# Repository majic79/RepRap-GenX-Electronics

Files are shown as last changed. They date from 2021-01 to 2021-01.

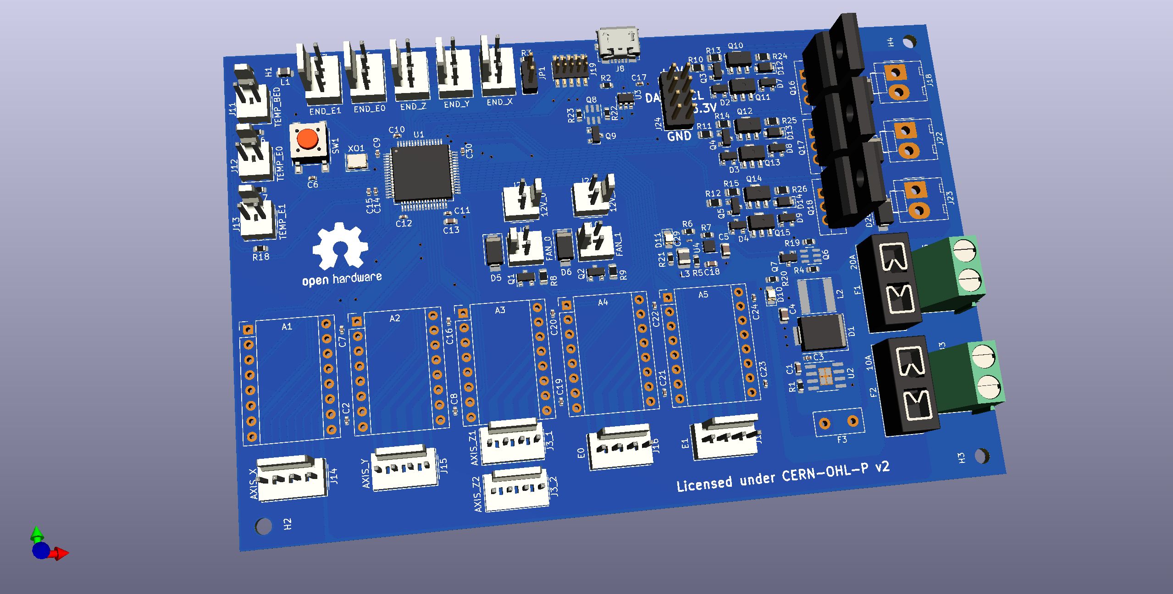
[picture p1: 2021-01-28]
RepRap_GenX_Electronics.png

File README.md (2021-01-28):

# RepRap GenX Electronics

## About
This project contains the hardware schematics and design choices for a low cost printer control board for RepRap hardware. Current boards are very capable, but make decisions on cost and feature set that are not of my choice. By making this available, I aim to add another option out there.

Making the printer control a drop in selection, this will permit re-use of existing driver breakouts (e.g. Pololu A4988's and DRV8825's) and with SPI support for TMC2300 breakouts, it allows an upgrade path. and low cost upgrade potential for existing printer controllers.

__!! Warning - this is still work in progress !!__

This board is based around the ARM MCU STM32F412RGT running at 96MHz in a LQFP-64 package. There are a few free pins, and with some ingenuity, some pins can be multiplexed/multi use.

## Plans

Future intent is to port MarlinFW to this package, from the PlatformIO platform. Programmers for these devices are relatively cheap, but there remains the possibility of a 0 cost programming option via the USB DFU device capabilties.

Selling these individually is not possible in todays marketplace without some additional testing and regulation, but those requirements need to be investigated and addressed as development progresses.

As the majority of components are surface mount (SMD) with only a few through-hole components, the plan is to complete the bill of materials (BOM) for the SMD components and send for professional fabrication on the prototypes.

## Milestones

  * ~~Initial Circuit~~
  * ~~MCU Selection~~
  * ~~Power Supplies~~
  * ~~PCB Layout~~
  * ~~RaspberryPi interface~~ (Abandoned due to lack of space for an interface)
  * ~~5V Power Output (on 2.54mm pitch 2x2 connector)~~
  * Review
  * Feedback
  * Component Selection (BOM)
  * Fabrication
  * Testing
  * Firmware Development

## News

### 2020-01-28
  - Added 3.3v and I2C to the breakout port for possible expansion
  - Shifted E0/E1 Filament sensor feedback to make room for I2C port
  - Adjusted some routes for the 2x4 breakout port

### 2020-01-26
  - Added totem pole drivers for the heater MOSFET's - switching time is <1uS so it should be possible to drive at 1MHz frequency if ever needed
  - Altered heater LED indicators to Red
  - Validated Fan PWM MOSFET's - 4mA is enough to drive at around 4uS which is plenty fast enough and won't overload GPIO pins
  - Altered layout to accomodate new components
  - Split MCU controlled components into their own sheet - not enough space on a single sheet for everything!

### 2020-01-21
  - Abandoned the idea of putting in a Pi Interface - difficult to maintain a 2 layer design and route everything for the 2x20pin GPIO interface of the Pi
  - Added ZVD Ideal diode for 5V output
  - Exposed 5V output (after ZVD) for external consumption (e.g. powering a Pi)
  - Added a copper pour on the top layer for an Earth plane
  - Re-Routed a few signals to maximise covered area on pour
  - Upped trace size for power lines to 0.8mm

### 2020-01-19
	- Initial Commit

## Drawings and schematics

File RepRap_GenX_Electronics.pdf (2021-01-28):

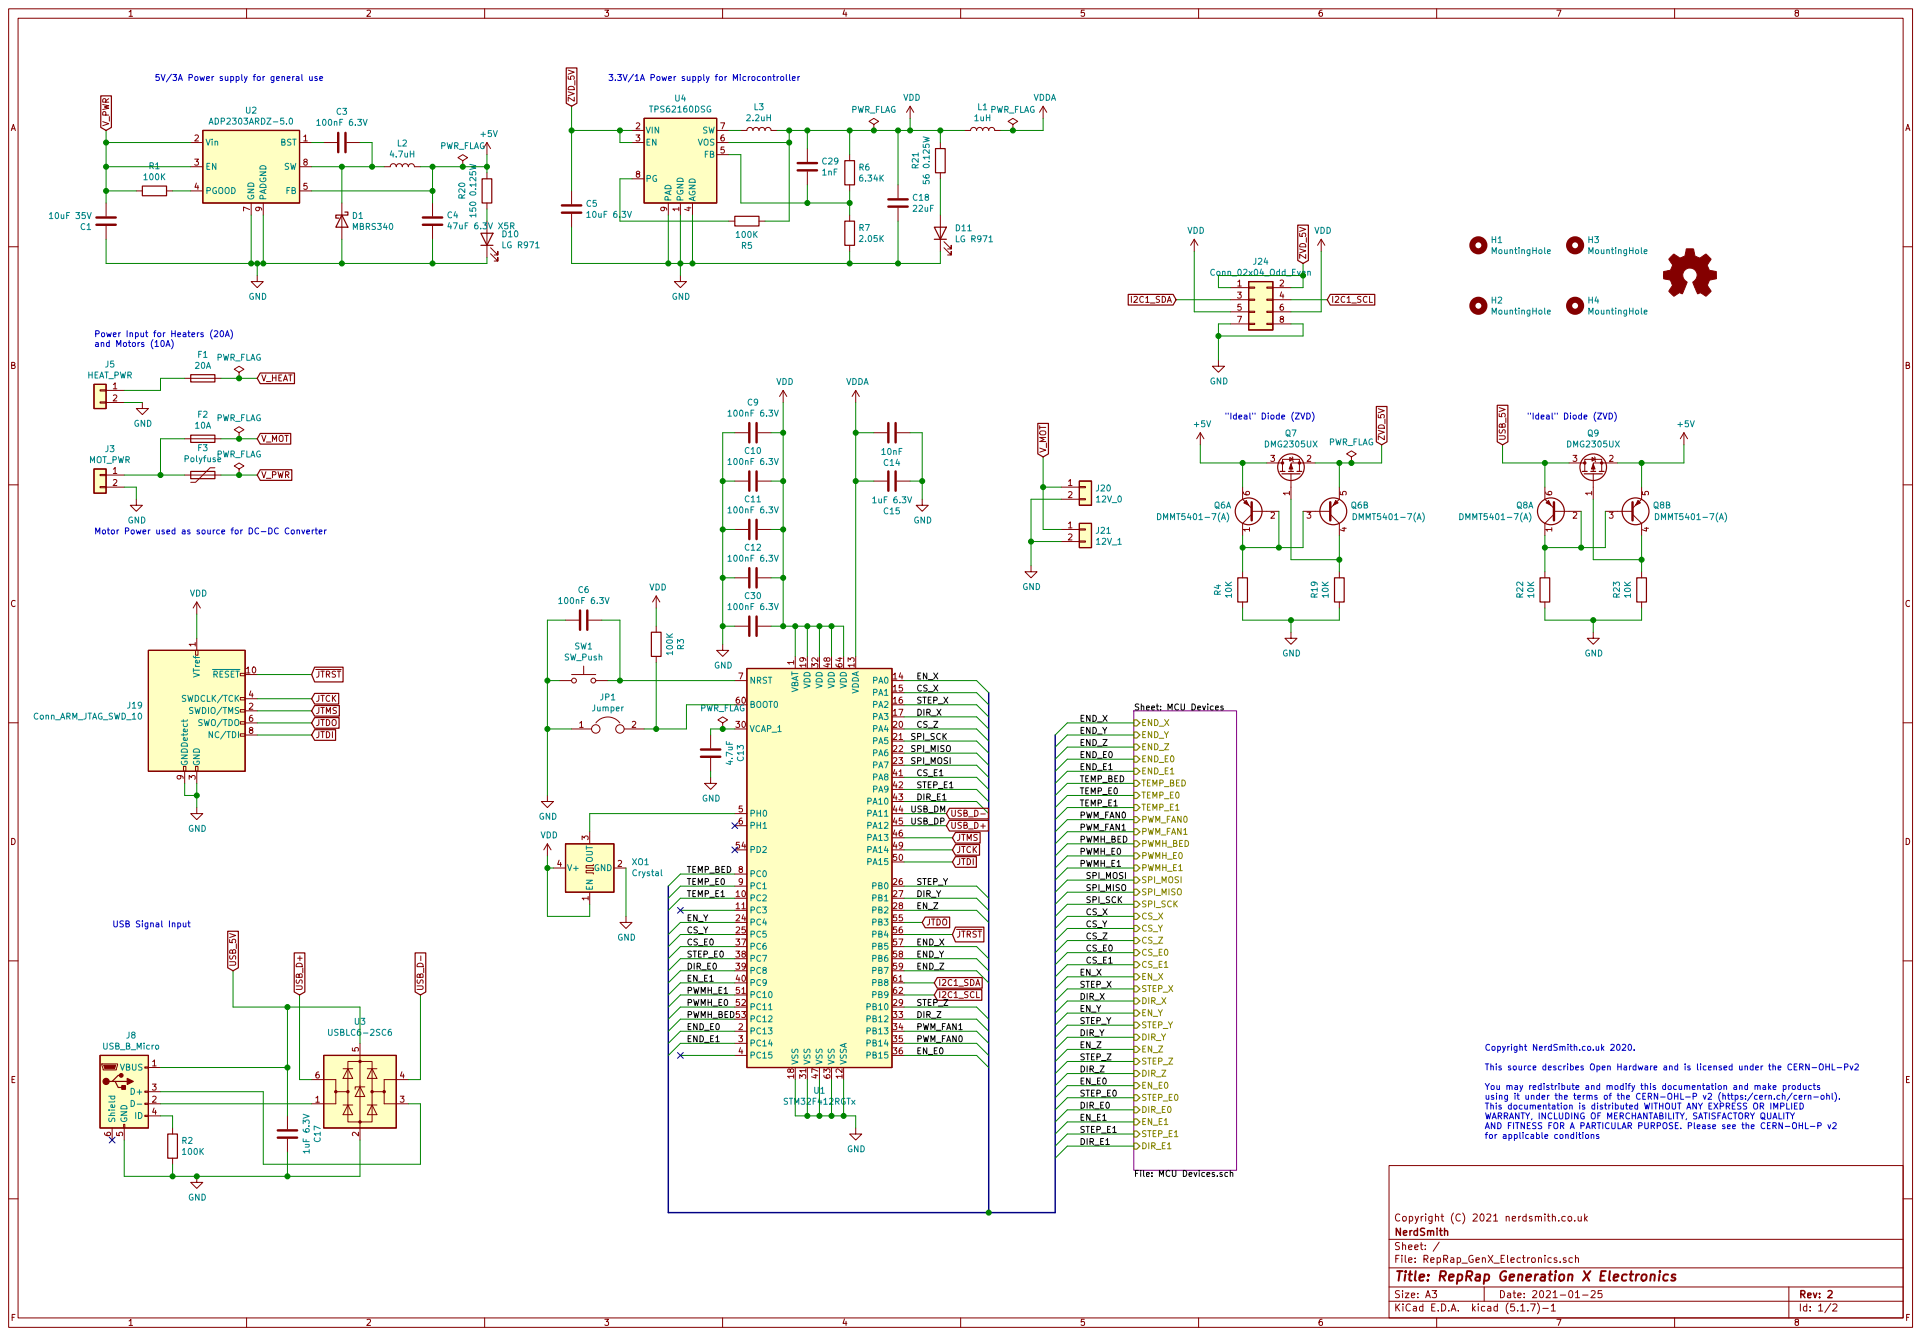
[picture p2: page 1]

5V/3A Power supply for general use

4 FB 5 VOS 6 SW 7 PG 8 PAD

Power Input for Heaters (20A)
and Motors (10A)

1 VCAP_1 30 VDD 19 VDD 32 VDD 48 VDD 64 VDDA 13 VSS 18 VSS 31 VSS 47 VSS 63 VSSA 12 U1 STM32F412RGTx

DIR_E1 EN_X DIR_X CS_X
Sheet: MCU Devices File: MCU Devices.sch
PWMH_E0 PWMH_E1 END_X

3 SWDCLK/TCK 4 SWO/TDO 6 NC/TDI 8 GNDDetect 9

This source describes Open Hardware and is licensed under the CERN-OHL-Pv2

You may redistribute and modify this documentation and make products
using it under the terms of the CERN-OHL-P v2 (https:/cern.ch/cern-ohl). This documentation is distributed WITHOUT ANY EXPRESS OR IMPLIED WARRANTY, INCLUDING OF MERCHANTABILITY, SATISFACTORY QUALITY

AND FITNESS FOR A PARTICULAR PURPOSE. Please see the CERN-OHL-P v2
for applicable conditions

File: RepRap_GenX_Electronics.sch Sheet: / NerdSmith Copyright (C) 2021 nerdsmith.co.uk

Id: 1/2 Title: RepRap Generation X Electronics

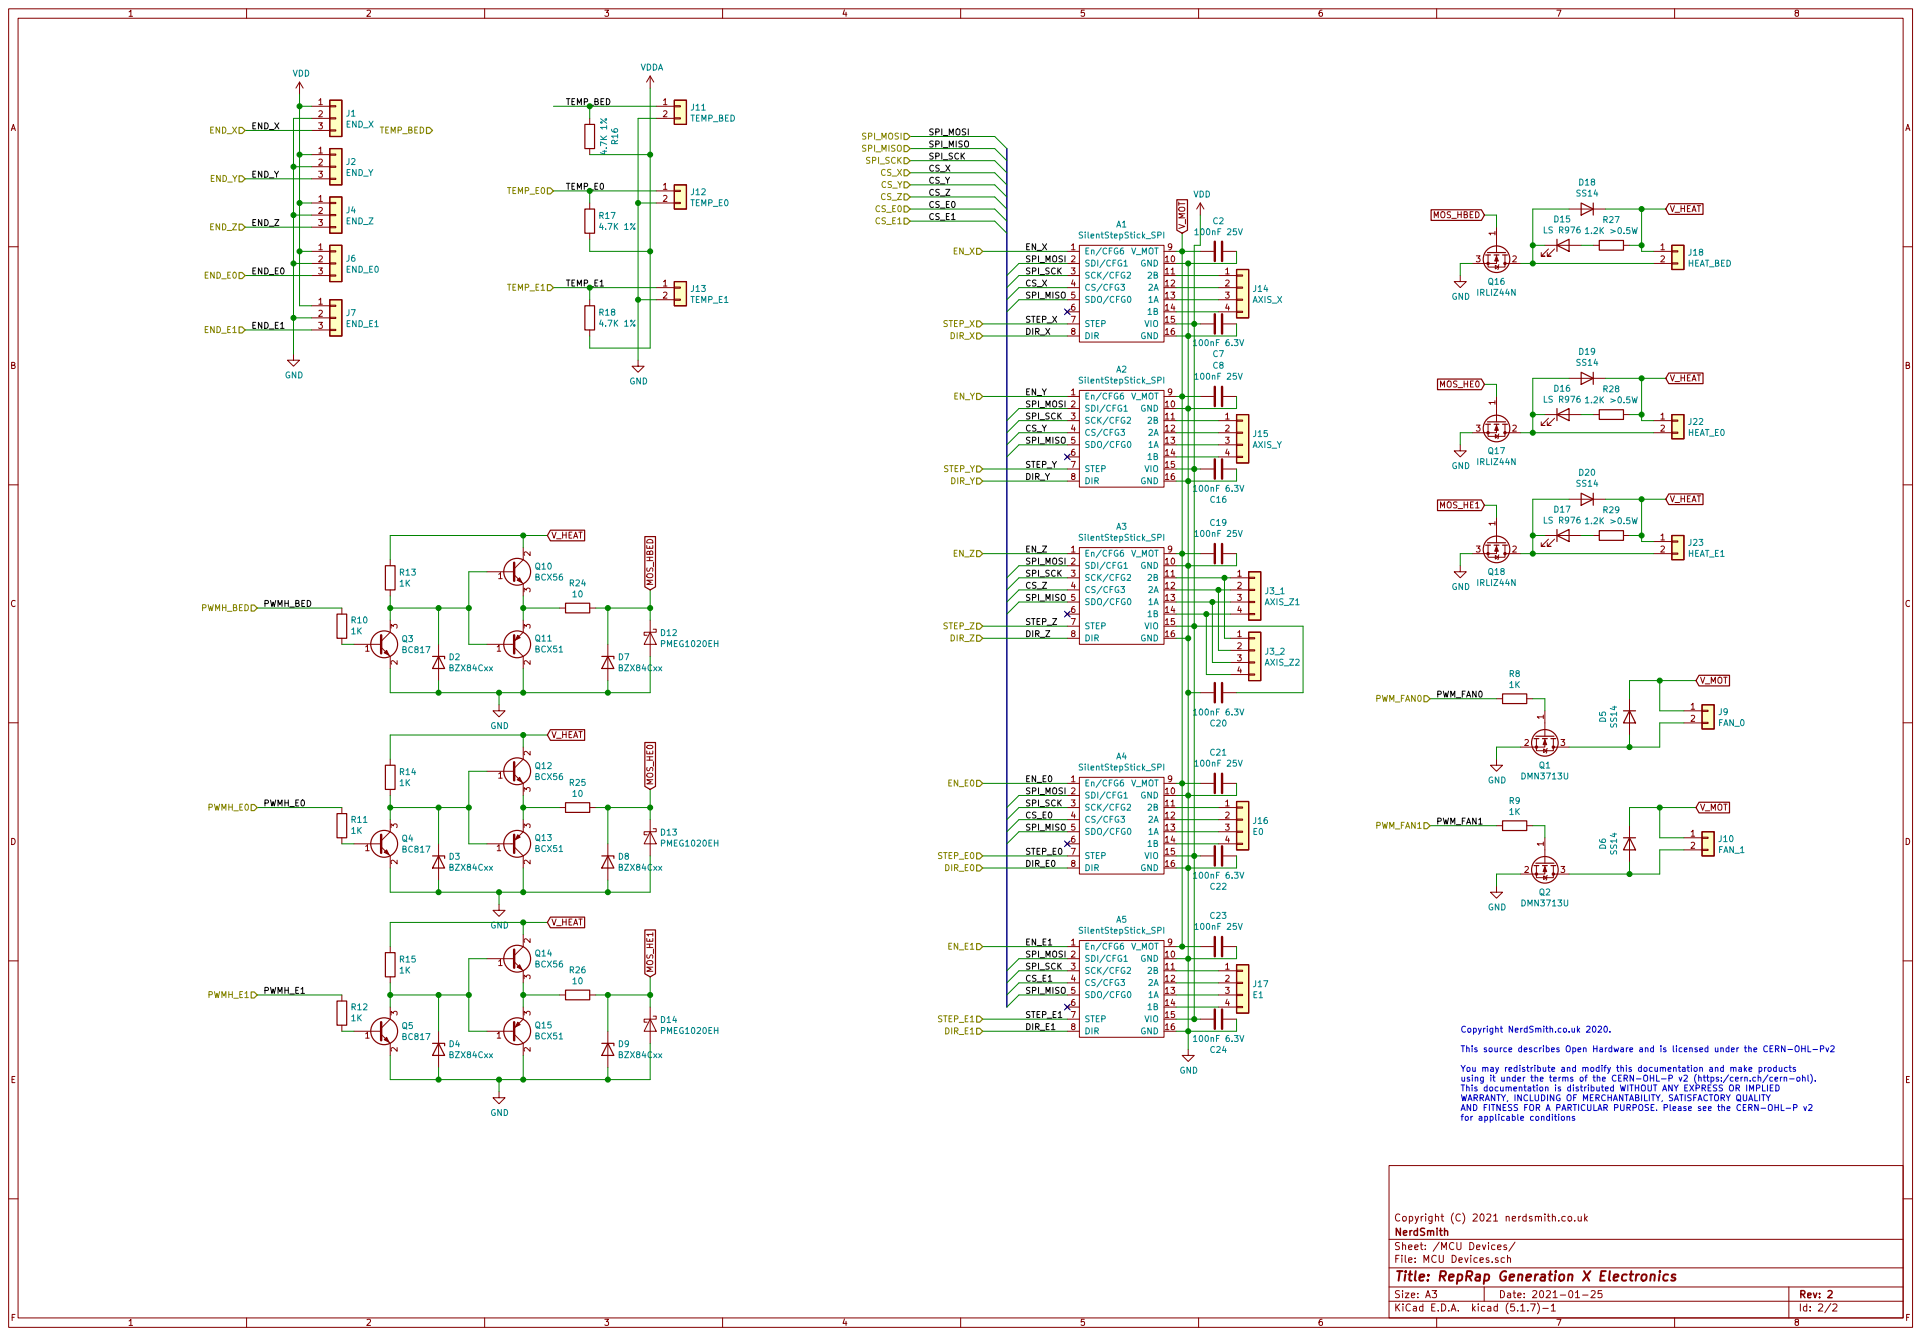
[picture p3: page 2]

This source describes Open Hardware and is licensed under the CERN-OHL-Pv2

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

AND FITNESS FOR A PARTICULAR PURPOSE. Please see the CERN-OHL-P v2
for applicable conditions

File: MCU Devices.sch Sheet: /MCU Devices/ NerdSmith Copyright (C) 2021 nerdsmith.co.uk

Id: 2/2 Title: RepRap Generation X Electronics

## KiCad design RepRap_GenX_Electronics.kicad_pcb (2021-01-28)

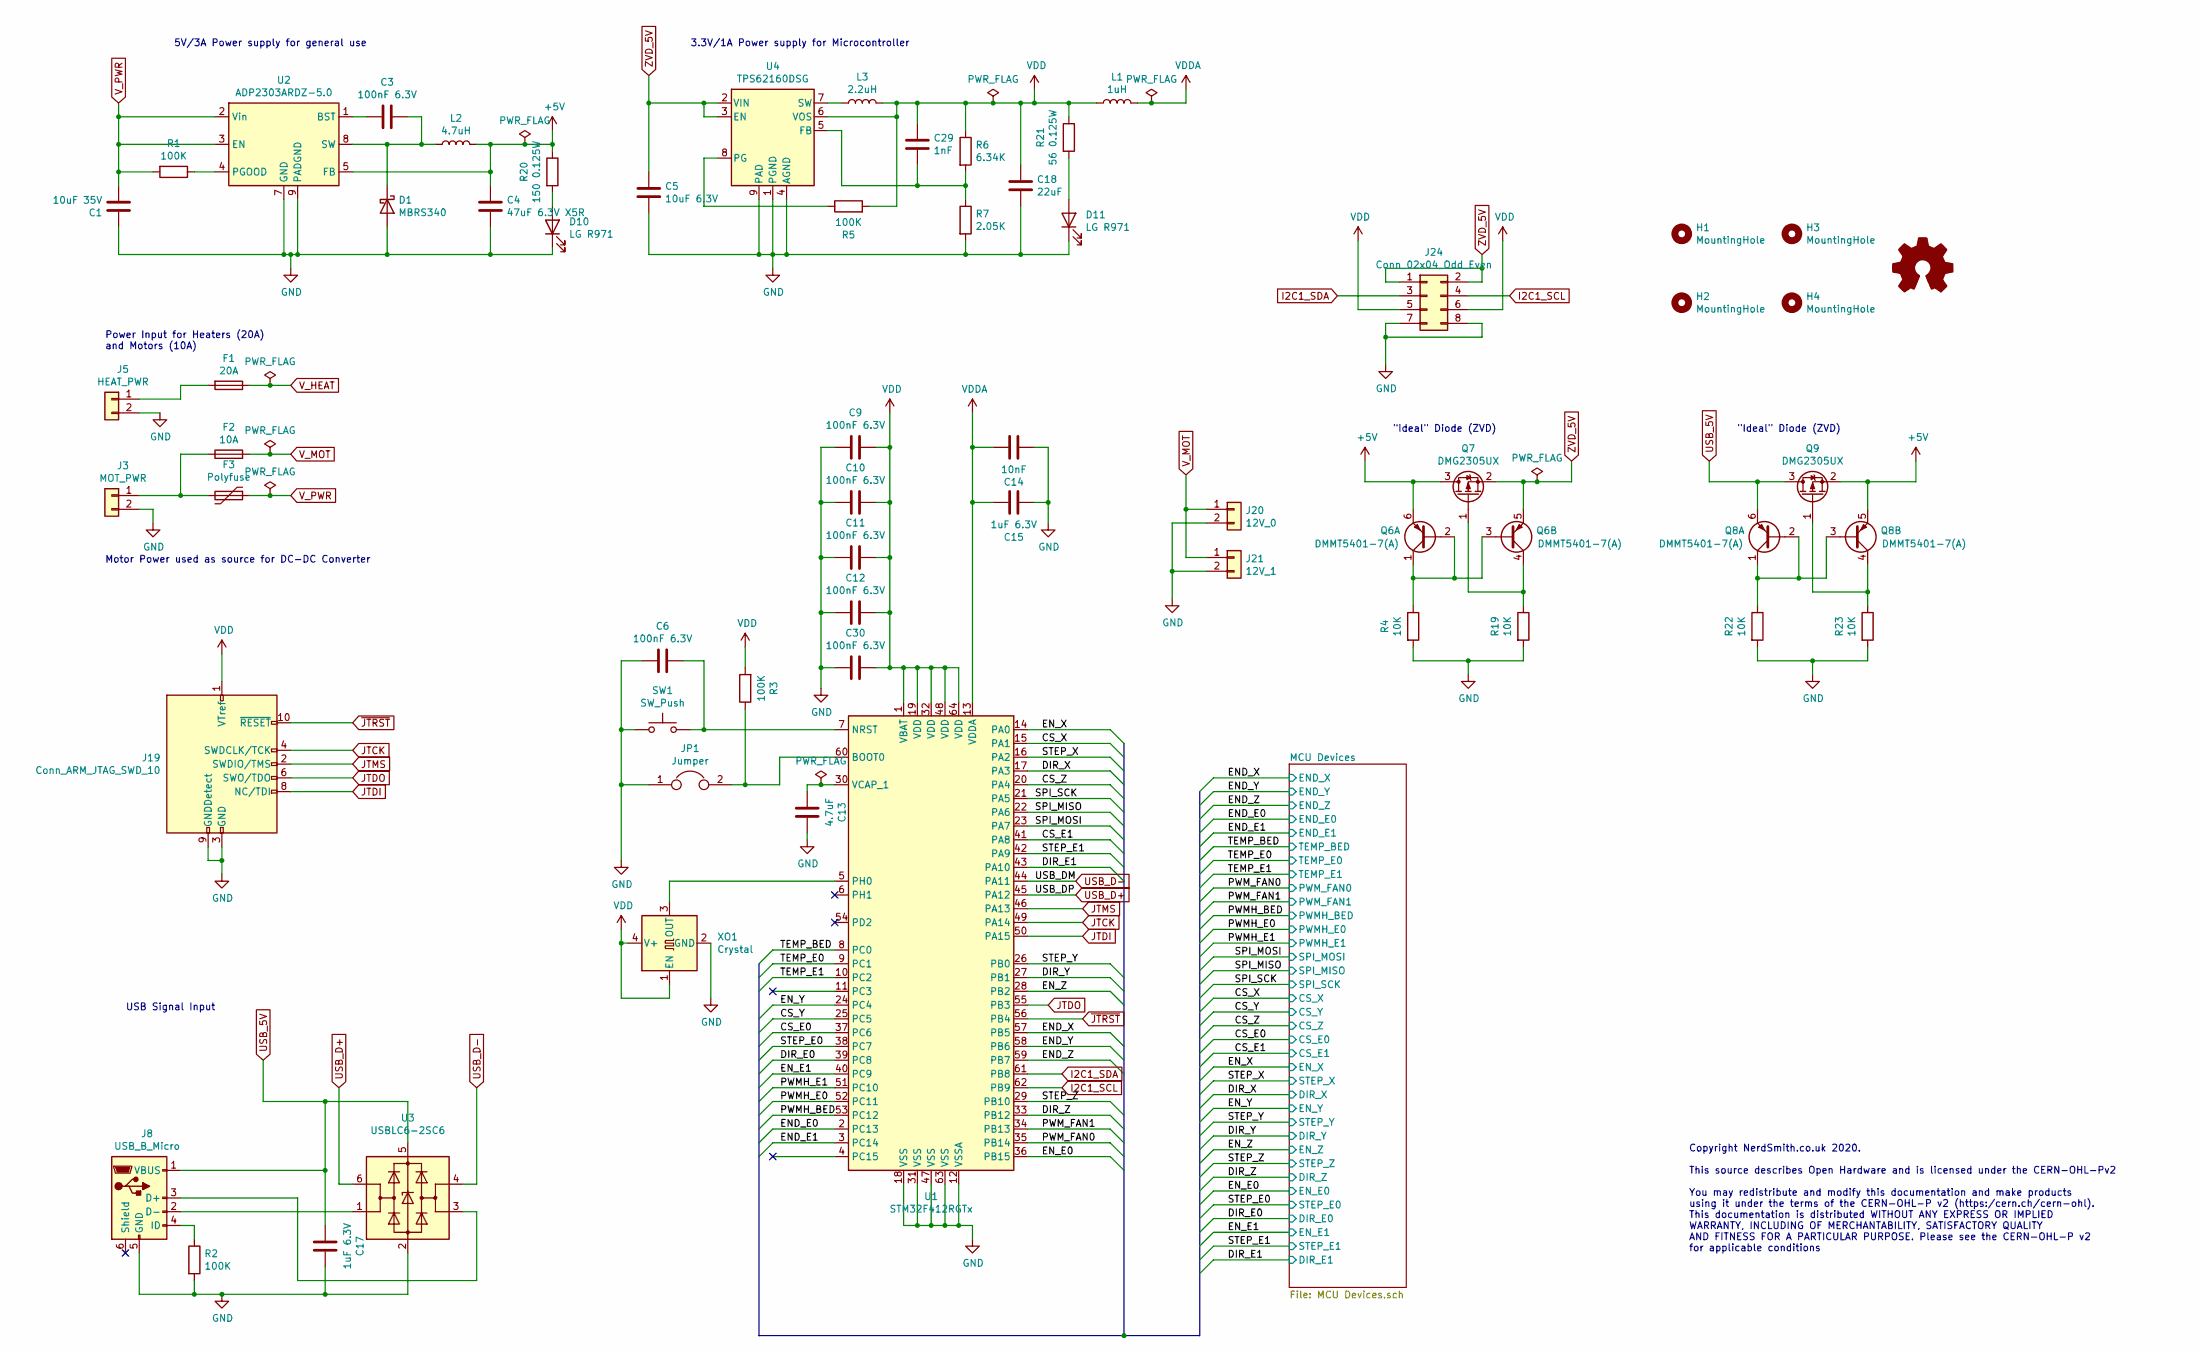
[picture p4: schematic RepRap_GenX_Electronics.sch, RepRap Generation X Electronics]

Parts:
C1: 10uF 35V; C_0603_1608Metric
C3, C6, C9, C10, C11, C12, C30: 100nF 6.3V; C_0402_1005Metric
C4: 47uF 6.3V X5R; C_0805_2012Metric; Mfr PartNumber JMK212BBJ476MG-T
C5: 10uF 6.3V; C_0805_2012Metric
C13: 4.7uF; C_0603_1608Metric
C14: 10nF; C_0402_1005Metric
C15, C17: 1uF 6.3V; C_0402_1005Metric
C18: 22uF; C_0603_1608Metric
C29: 1nF; C_0201_0603Metric
D1: MBRS340; D_SMC; Mfr PartNumber MBRS340T3G
D10, D11: LG R971; LED_0805_2012Metric_Castellated
F1: 20A; Fuseholder_Blade_Mini_Keystone_3568
F2: 10A; Fuseholder_Blade_Mini_Keystone_3568
F3: Polyfuse; Fuse_Littelfuse_395Series; Mfr PartNumber RF2624-000
G1: Logo_Open_Hardware_Small; OSHW-Logo2_14.6x12mm_SilkScreen
H1, H2, H3, H4: MountingHole; MountingHole_2.7mm_M2.5_ISO14580
J3: MOT_PWR; TerminalBlock_Phoenix_MKDS-1,5-2-5.08_1x02_P5.08mm_Horizont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
J5: HEAT_PWR; TerminalBlock_Phoenix_MKDS-1,5-2-5.08_1x02_P5.08mm_Horizont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
J8: USB_B_Micro; USB_Micro-B_Molex_47346-0001; Mfr PartNumber 47346-0001
J19: Conn_ARM_JTAG_SWD_10; PinHeader_2x05_P1.27mm_Vertical_SMD; Mfr PartNumber M50-3600542
J20: 12V_0; Molex_KK-254_AE-6410-02A_1x02_P2.54mm_Vertical
J21: 12V_1; Molex_KK-254_AE-6410-02A_1x02_P2.54mm_Vertical
J24: Conn_02x04_Odd_Even; PinHeader_2x04_P2.54mm_Vertical
JP1: Jumper; PinHeader_1x02_P2.54mm_Vertical
L1: 1uH; L_0805_2012Metric; Mfr PartNumber MLZ2012A1R0MT
L2: 4.7uH; L_Taiyo-Yuden_NR-60xx; Mfr PartNumber 74406043047
L3: 2.2uH; L_1008_2520Metric_Pad1.43x2.20mm_HandSolder; Mfr PartNumber VLS252012CX-2R2M-1
Q6, Q8: DMMT5401-7(A); SC-74-6_1.5x2.9mm_P0.95mm; Mfr PartNumber DMMT5401
Q7, Q9: DMG2305UX; SOT-23; Mfr PartNumber DMG2305UX
R1, R2, R3, R5: 100K; R_0603_1608Metric
R4, R19, R22, R23: 10K; R_0603_1608Metric
R6: 6.34K; R_0603_1608Metric
R7: 2.05K; R_0603_1608Metric
R20: 150 0.125W; R_0603_1608Metric
R21: 56 0.125W; R_0603_1608Metric
SW1: SW_Push; SW_SPST_PTS645; Mfr PartNumber PTS645SK43SMTR 92 LFS
U1: STM32F412RGTx; LQFP-64_10x10mm_P0.5mm; Mfr PartNumber STM32F412RGT6
U2: ADP2303ARDZ-5.0; SOIC-8-1EP_3.9x4.9mm_P1.27mm_EP2.29x3mm_ThermalVias; Mfr PartNumber ADP2302ARDZ-5.0
U3: USBLC6-2SC6; SOT-23-6; Mfr PartNumber USBLC6-2SC6
U4: TPS62160DSG; WSON-8-1EP_2x2mm_P0.5mm_EP0.9x1.6mm_ThermalVias; Mfr PartNumber TPS62160DSG
XO1: Crystal; Crystal_SMD_3225-4Pin_3.2x2.5mm; Mfr PartNumber Q33519E40001912

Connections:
+5V: C4.2, L2.2, Q6.6 (E1), Q7.3 (D), Q8.5 (E2), Q9.2 (S), R20.1, U2.5 (FB)
/CS_E0: U1.37 (PC6); also elsewhere on the board
/CS_E1: U1.41 (PA8); also elsewhere on the board
/CS_X: U1.15 (PA1); also elsewhere on the board
/CS_Y: U1.25 (PC5); also elsewhere on the board
/CS_Z: U1.20 (PA4); also elsewhere on the board
/DIR_E0: U1.39 (PC8); also elsewhere on the board
/DIR_E1: U1.43 (PA10); also elsewhere on the board
/DIR_X: U1.17 (PA3); also elsewhere on the board
/DIR_Y: U1.27 (PB1); also elsewhere on the board
/DIR_Z: U1.33 (PB12); also elsewhere on the board
/END_E0: U1.2 (PC13); also elsewhere on the board
/END_E1: U1.3 (PC14); also elsewhere on the board
/END_X: U1.57 (PB5); also elsewhere on the board
/END_Y: U1.58 (PB6); also elsewhere on the board
/END_Z: U1.59 (PB7); also elsewhere on the board
/EN_E0: U1.36 (PB15); also elsewhere on the board
/EN_E1: U1.40 (PC9); also elsewhere on the board
/EN_X: U1.14 (PA0); also elsewhere on the board
/EN_Y: U1.24 (PC4); also elsewhere on the board
/EN_Z: U1.28 (PB2); also elsewhere on the board
/PWMH_BED: U1.53 (PC12); also elsewhere on the board
/PWMH_E0: U1.52 (PC11); also elsewhere on the board
/PWMH_E1: U1.51 (PC10); also elsewhere on the board
/PWM_FAN0: U1.35 (PB14); also elsewhere on the board
/PWM_FAN1: U1.34 (PB13); also elsewhere on the board
/SPI_MISO: U1.22 (PA6); also elsewhere on the board
/SPI_MOSI: U1.23 (PA7); also elsewhere on the board
/SPI_SCK: U1.21 (PA5); also elsewhere on the board
/STEP_E0: U1.38 (PC7); also elsewhere on the board
/STEP_E1: U1.42 (PA9); also elsewhere on the board
/STEP_X: U1.16 (PA2); also elsewhere on the board
/STEP_Y: U1.26 (PB0); also elsewhere on the board
/STEP_Z: U1.29 (PB10); also elsewhere on the board
/TEMP_BED: U1.8 (PC0); also elsewhere on the board
/TEMP_E0: U1.9 (PC1); also elsewhere on the board
/TEMP_E1: U1.10 (PC2); also elsewhere on the board
GND: C1.2, C4.1, C5.2, C6.2, C9.2, C10.2, C11.2, C12.2, C13.1, C14.2, C15.2, C17.1, C18.2, C30.2, D1.2 (A), D10.1 (K), D11.1 (K), J3.2, J5.2, J8.5 (GND), J19.3 (GND), J19.5 (GND), J19.9 (GNDDetect), J20.2, J21.2, J24.7, J24.8, JP1.1, R2.2, R4.2, R7.2, R19.2, R22.2, R23.2, SW1.1, U1.12 (VSSA), U1.18 (VSS), U1.31 (VSS), U1.47 (VSS), U1.63 (VSS), U2.7 (GND), U2.9 (PADGND), U3.2 (GND), U4.1 (PGND), U4.4 (AGND), U4.9 (PAD), XO1.2 (GND); also elsewhere on the board
I2C1_SCL: J24.4, U1.62 (PB9)
I2C1_SDA: J24.3, U1.61 (PB8)
JTCK: J19.4 (SWDCLK/TCK), U1.49 (PA14)
JTDI: J19.8 (NC/TDI), U1.50 (PA15)
JTDO: J19.6 (SWO/TDO), U1.55 (PB3)
JTMS: J19.2 (SWDIO/TMS), U1.46 (PA13)
unnamed: C3.1, U2.1 (BST)
unnamed: C3.2, D1.1 (K), L2.1, U2.8 (SW)
unnamed: C6.1, SW1.2, U1.7 (NRST)
unnamed: C13.2, U1.30 (VCAP_1)
unnamed: C29.2, R6.2, R7.1, U4.5 (FB)
unnamed: D10.2 (A), R20.2
unnamed: D11.2 (A), R21.2
unnamed: F1.2, J5.1
unnamed: F2.1, F3.2, J3.1
unnamed: J8.2 (D-), U3.1 (I/O1)
unnamed: J8.3 (D+), U3.3 (I/O2)
unnamed: J8.4 (ID), R2.1
unnamed: JP1.2, R3.1, U1.60 (BOOT0)
unnamed: L3.1, U4.7 (SW)
unnamed: Q6.1 (C1), Q6.2 (B1), Q6.3 (B2), R4.1
unnamed: Q6.4 (C2), Q7.1 (G), R19.1
unnamed: Q8.1 (C1), Q8.2 (B1), Q8.3 (B2), R22.1
unnamed: Q8.4 (C2), Q9.1 (G), R23.1
unnamed: R1.1, U2.4 (PGOOD)
unnamed: R5.1, U4.8 (PG)
unnamed: U1.5 (PH0), XO1.3 (OUT)
USB_5V: C17.2, J8.1 (VBUS), Q8.6 (E1), Q9.3 (D), U3.5 (VBUS)
USB_D+: U1.45 (PA12), U3.6 (I/O1)
USB_D-: U1.44 (PA11), U3.4 (I/O2)
VDD: C9.1, C10.1, C11.1, C12.1, C18.1, C29.1, C30.1, J19.1 (VTref), J24.5, J24.6, L1.1, L3.2, R3.2, R5.2, R6.1, R21.1, U1.1 (VBAT), U1.19 (VDD), U1.32 (VDD), U1.48 (VDD), U1.64 (VDD), U4.6 (VOS), XO1.1 (EN), XO1.4 (V+); also elsewhere on the board
VDDA: C14.1, C15.1, L1.2, U1.13 (VDDA); also elsewhere on the board
V_HEAT: F1.1; also elsewhere on the board
V_MOT: F2.2, J20.1, J21.1; also elsewhere on the board
V_PWR: C1.1, F3.1, R1.2, U2.2 (Vin), U2.3 (EN)
ZVD_5V: C5.1, J24.1, J24.2, Q6.5 (E2), Q7.2 (S), U4.2 (VIN), U4.3 (EN)
~JTRST: J19.10 (~RESET~), U1.56 (PB4)

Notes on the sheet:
5V/3A Power supply for general use
3.3V/1A Power supply for Microcontroller
USB Signal Input
Power Input for Heaters (20A) and Motors (10A)
Motor Power used as source for DC-DC Converter
"Ideal" Diode (ZVD)
Copyright NerdSmith.co.uk 2020. This source describes Open Hardware and is licensed under the CERN-OHL-Pv2 You may redistribute and modify this documentation and make products using it under the terms of the CERN-OHL-P v2 (https:/cern.ch/cern-ohl). This documentation is distributed WITHOUT ANY EXPR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

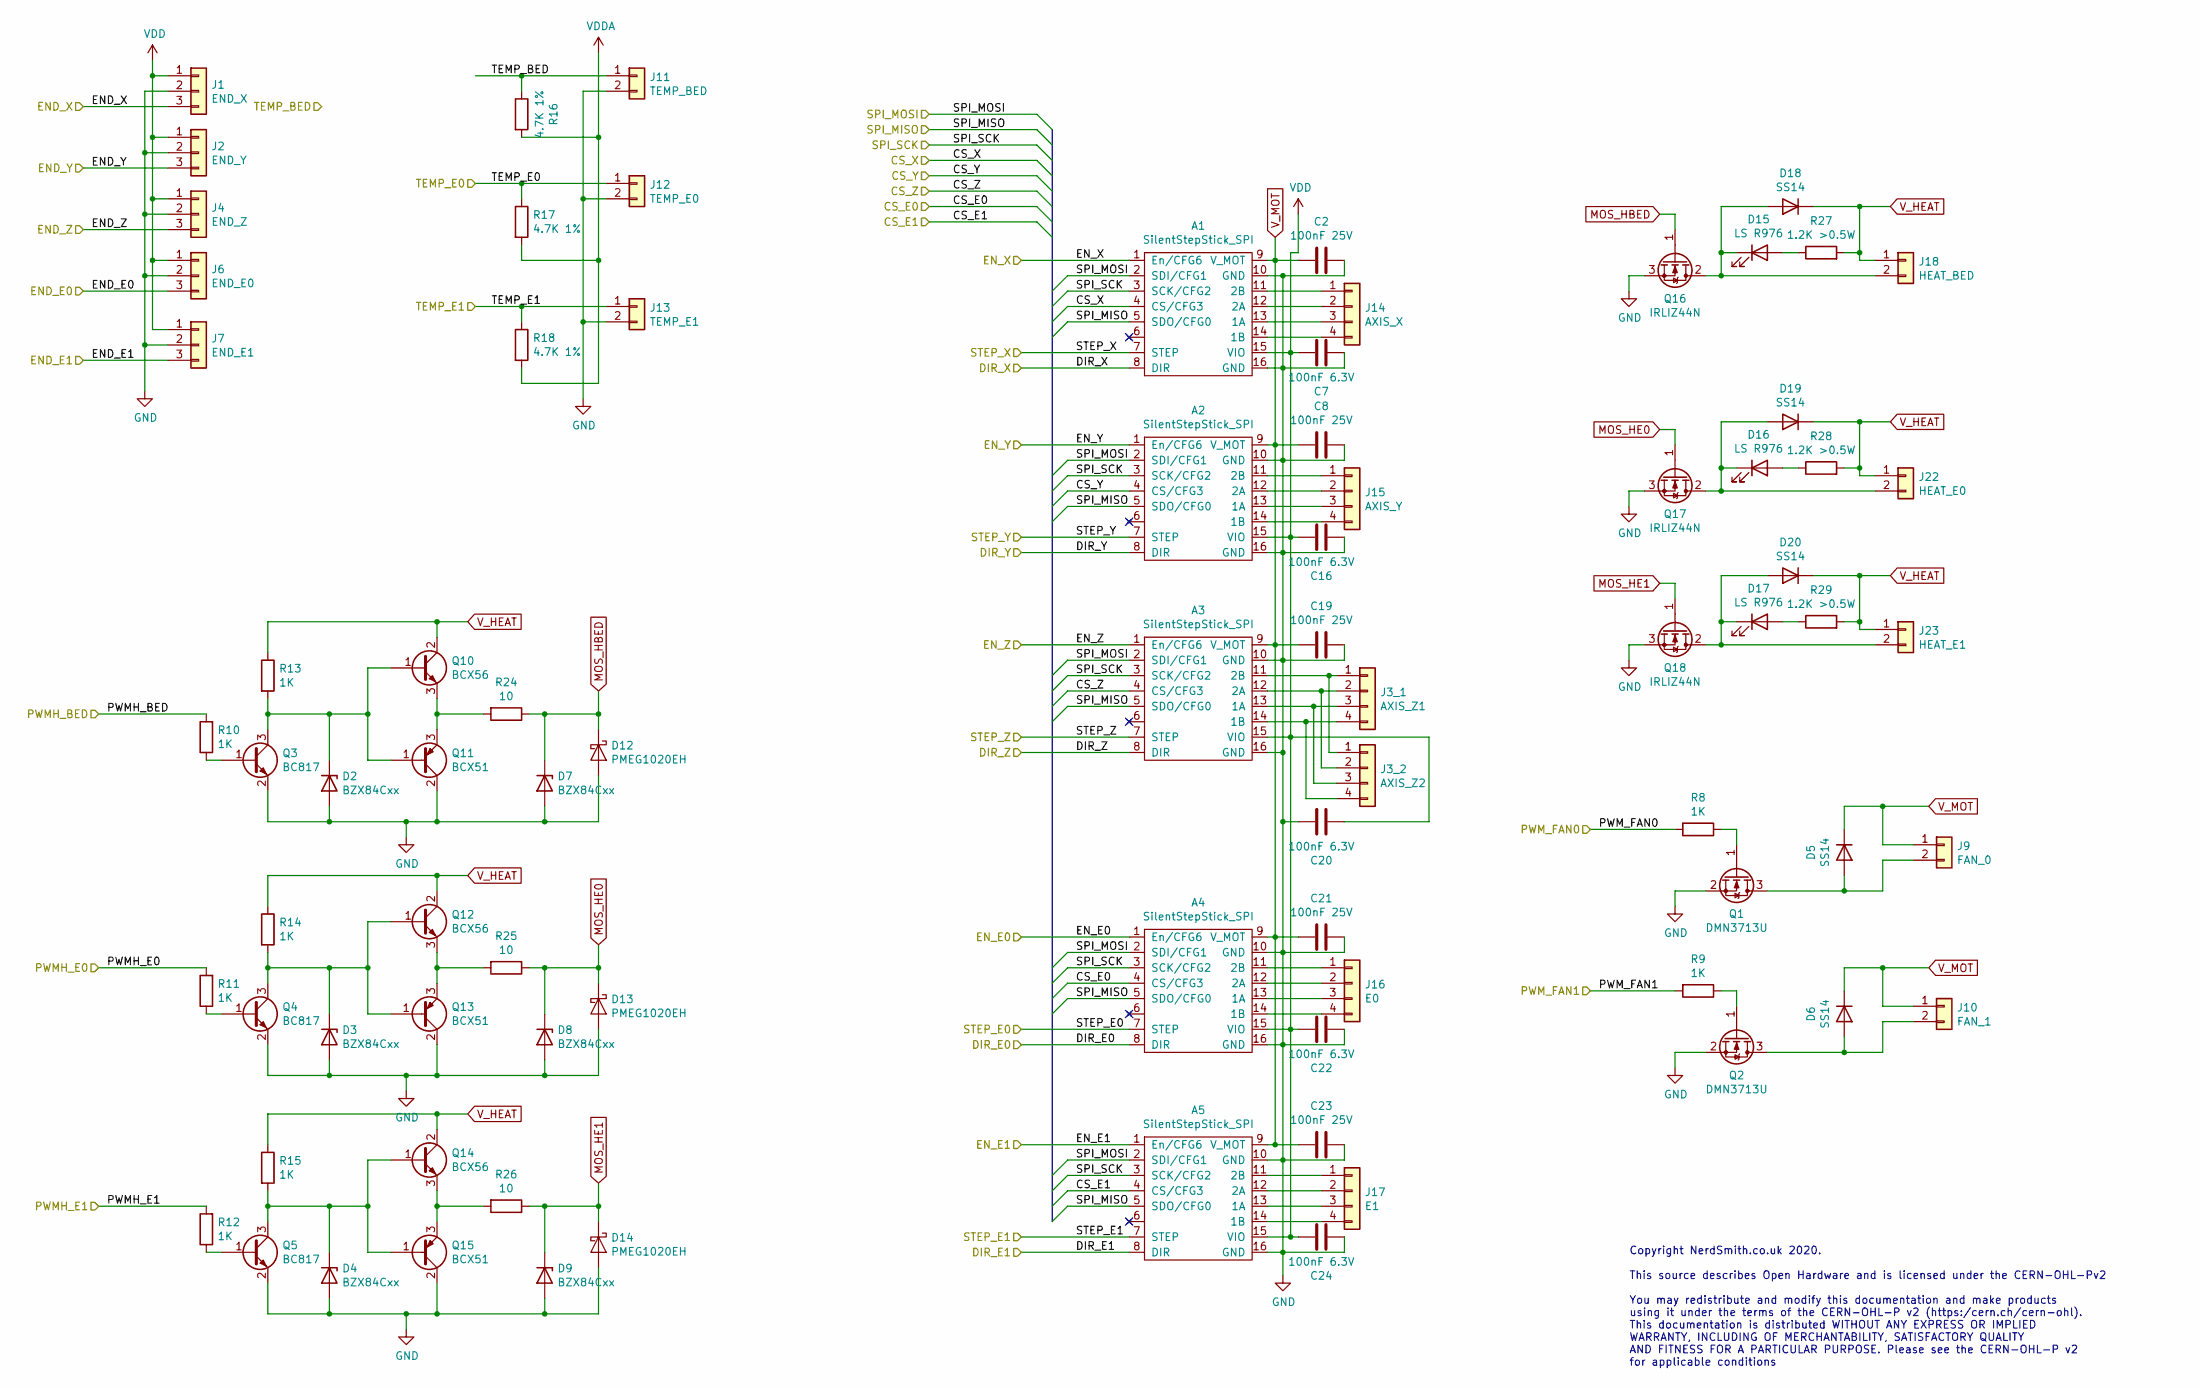
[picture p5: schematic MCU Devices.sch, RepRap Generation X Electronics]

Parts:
A1, A2, A3, A4, A5: SilentStepStick_SPI; Pololu_Breakout-16_15.2x20.3mm
C2, C8, C19, C21, C23: 100nF 25V; C_0402_1005Metric
C7, C16, C20, C22, C24: 100nF 6.3V; C_0402_1005Metric
D2, D3, D4, D7, D8, D9: BZX84Cxx; D_SOT-23_ANK
D5, D6, D18, D19, D20: SS14; D_SMA; Mfr PartNumber SS14
D12, D13, D14: PMEG1020EH; D_SOD-123F
D15, D16, D17: LS R976; LED_0805_2012Metric_Castellated
J1: END_X; Molex_KK-254_AE-6410-03A_1x03_P2.54mm_Vertical
J2: END_Y; Molex_KK-254_AE-6410-03A_1x03_P2.54mm_Vertical
J3_1: AXIS_Z1; Molex_KK-254_AE-6410-04A_1x04_P2.54mm_Vertical
J3_2: AXIS_Z2; Molex_KK-254_AE-6410-04A_1x04_P2.54mm_Vertical
J4: END_Z; Molex_KK-254_AE-6410-03A_1x03_P2.54mm_Vertical
J6: END_E0; Molex_KK-254_AE-6410-03A_1x03_P2.54mm_Vertical
J7: END_E1; Molex_KK-254_AE-6410-03A_1x03_P2.54mm_Vertical
J9: FAN_0; Molex_KK-254_AE-6410-02A_1x02_P2.54mm_Vertical
J10: FAN_1; Molex_KK-254_AE-6410-02A_1x02_P2.54mm_Vertical
J11: TEMP_BED; Molex_KK-254_AE-6410-02A_1x02_P2.54mm_Vertical
J12: TEMP_E0; Molex_KK-254_AE-6410-02A_1x02_P2.54mm_Vertical
J13: TEMP_E1; Molex_KK-254_AE-6410-02A_1x02_P2.54mm_Vertical
J14: AXIS_X; Molex_KK-254_AE-6410-04A_1x04_P2.54mm_Vertical
J15: AXIS_Y; Molex_KK-254_AE-6410-04A_1x04_P2.54mm_Vertical
J16: E0; Molex_KK-254_AE-6410-04A_1x04_P2.54mm_Vertical
J17: E1; Molex_KK-254_AE-6410-04A_1x04_P2.54mm_Vertical
J18: HEAT_BED; Molex_KK-396_A-41791-0002_1x02_P3.96mm_Vertical
J22: HEAT_E0; Molex_KK-396_A-41791-0002_1x02_P3.96mm_Vertical
J23: HEAT_E1; Molex_KK-396_A-41791-0002_1x02_P3.96mm_Vertical
Q1, Q2: DMN3713U; SOT-23; Mfr PartNumber DMN3713U
Q3, Q4, Q5: BC817; SOT-23
Q10, Q12, Q14: BCX56; SOT-89-3
Q11, Q13, Q15: BCX51; SOT-89-3
Q16, Q17, Q18: IRLIZ44N; TO-220F-3_Vertical
R8, R9, R10, R11, R12, R13, R14, R15: 1K; R_0805_2012Metric
R16, R17, R18: 4.7K 1%; R_0603_1608Metric
R24, R25, R26: 10; R_0805_2012Metric
R27, R28, R29: 1.2K >0.5W; R_2010_5025Metric

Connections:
/CS_E0: A4.4 (CS/CFG3); also elsewhere on the board
/CS_E1: A5.4 (CS/CFG3); also elsewhere on the board
/CS_X: A1.4 (CS/CFG3); also elsewhere on the board
/CS_Y: A2.4 (CS/CFG3); also elsewhere on the board
/CS_Z: A3.4 (CS/CFG3); also elsewhere on the board
/DIR_E0: A4.8 (DIR); also elsewhere on the board
/DIR_E1: A5.8 (DIR); also elsewhere on the board
/DIR_X: A1.8 (DIR); also elsewhere on the board
/DIR_Y: A2.8 (DIR); also elsewhere on the board
/DIR_Z: A3.8 (DIR); also elsewhere on the board
/END_E0: J6.3; also elsewhere on the board
/END_E1: J7.3; also elsewhere on the board
/END_X: J1.3; also elsewhere on the board
/END_Y: J2.3; also elsewhere on the board
/END_Z: J4.3; also elsewhere on the board
/EN_E0: A4.1 (En/CFG6); also elsewhere on the board
/EN_E1: A5.1 (En/CFG6); also elsewhere on the board
/EN_X: A1.1 (En/CFG6); also elsewhere on the board
/EN_Y: A2.1 (En/CFG6); also elsewhere on the board
/EN_Z: A3.1 (En/CFG6); also elsewhere on the board
/PWMH_BED: R10.2; also elsewhere on the board
/PWMH_E0: R11.2; also elsewhere on the board
/PWMH_E1: R12.2; also elsewhere on the board
/PWM_FAN0: R8.2; also elsewhere on the board
/PWM_FAN1: R9.2; also elsewhere on the board
/SPI_MISO: A1.5 (SDO/CFG0), A2.5 (SDO/CFG0), A3.5 (SDO/CFG0), A4.5 (SDO/CFG0), A5.5 (SDO/CFG0); also elsewhere on the board
/SPI_MOSI: A1.2 (SDI/CFG1), A2.2 (SDI/CFG1), A3.2 (SDI/CFG1), A4.2 (SDI/CFG1), A5.2 (SDI/CFG1); also elsewhere on the board
/SPI_SCK: A1.3 (SCK/CFG2), A2.3 (SCK/CFG2), A3.3 (SCK/CFG2), A4.3 (SCK/CFG2), A5.3 (SCK/CFG2); also elsewhere on the board
/STEP_E0: A4.7 (STEP); also elsewhere on the board
/STEP_E1: A5.7 (STEP); also elsewhere on the board
/STEP_X: A1.7 (STEP); also elsewhere on the board
/STEP_Y: A2.7 (STEP); also elsewhere on the board
/STEP_Z: A3.7 (STEP); also elsewhere on the board
/TEMP_BED: J11.1, R16.1; also elsewhere on the board
/TEMP_E0: J12.1, R17.1; also elsewhere on the board
/TEMP_E1: J13.1, R18.1; also elsewhere on the board
GND: A1.10 (GND), A1.16 (GND), A2.10 (GND), A2.16 (GND), A3.10 (GND), A3.16 (GND), A4.10 (GND), A4.16 (GND), A5.10 (GND), A5.16 (GND), C2.1, C7.2, C8.2, C16.1, C19.2, C20.2, C21.2, C22.1, C23.2, C24.1, D2.2 (A), D3.2 (A), D4.2 (A), D7.2 (A), D8.2 (A), D9.2 (A), D12.2 (A), D13.2 (A), D14.2 (A), J1.2, J2.2, J4.2, J6.2, J7.2, J11.2, J12.2, J13.2, Q1.2 (S), Q2.2 (S), Q3.2 (E), Q4.2 (E), Q5.2 (E), Q11.2 (C), Q13.2 (C), Q15.2 (C), Q16.3 (S), Q17.3 (S), Q18.3 (S); also elsewhere on the board
MOS_HBED: D7.1 (K), D12.1 (K), Q16.1 (G), R24.1
MOS_HE0: D8.1 (K), D13.1 (K), Q17.1 (G), R25.1
MOS_HE1: D9.1 (K), D14.1 (K), Q18.1 (G), R26.1
unnamed: A1.11 (2B), J14.1
unnamed: A1.12 (2A), J14.2
unnamed: A1.13 (1A), J14.3
unnamed: A1.14 (1B), J14.4
unnamed: A2.11 (2B), J15.1
unnamed: A2.12 (2A), J15.2
unnamed: A2.13 (1A), J15.3
unnamed: A2.14 (1B), J15.4
unnamed: A3.11 (2B), J3_1.1, J3_2.1
unnamed: A3.12 (2A), J3_1.2, J3_2.2
unnamed: A3.13 (1A), J3_1.3, J3_2.3
unnamed: A3.14 (1B), J3_1.4, J3_2.4
unnamed: A4.11 (2B), J16.1
unnamed: A4.12 (2A), J16.2
unnamed: A4.13 (1A), J16.3
unnamed: A4.14 (1B), J16.4
unnamed: A5.11 (2B), J17.1
unnamed: A5.12 (2A), J17.2
unnamed: A5.13 (1A), J17.3
unnamed: A5.14 (1B), J17.4
unnamed: D2.1 (K), Q3.3 (C), Q10.1 (B), Q11.1 (B), R13.2
unnamed: D3.1 (K), Q4.3 (C), Q12.1 (B), Q13.1 (B), R14.2
unnamed: D4.1 (K), Q5.3 (C), Q14.1 (B), Q15.1 (B), R15.2
unnamed: D5.2 (A), J9.2, Q1.3 (D)
unnamed: D6.2 (A), J10.2, Q2.3 (D)
unnamed: D15.1 (K), D18.2 (A), J18.2, Q16.2 (D)
unnamed: D15.2 (A), R27.1
unnamed: D16.1 (K), D19.2 (A), J22.2, Q17.2 (D)
unnamed: D16.2 (A), R28.1
unnamed: D17.1 (K), D20.2 (A), J23.2, Q18.2 (D)
unnamed: D17.2 (A), R29.1
unnamed: Q1.1 (G), R8.1
unnamed: Q2.1 (G), R9.1
unnamed: Q3.1 (B), R10.1
unnamed: Q4.1 (B), R11.1
unnamed: Q5.1 (B), R12.1
unnamed: Q10.3 (E), Q11.3 (E), R24.2
unnamed: Q12.3 (E), Q13.3 (E), R25.2
unnamed: Q14.3 (E), Q15.3 (E), R26.2
VDD: A1.15 (VIO), A2.15 (VIO), A3.15 (VIO), A4.15 (VIO), A5.15 (VIO), C7.1, C16.2, C20.1, C22.2, C24.2, J1.1, J2.1, J4.1, J6.1, J7.1; also elsewhere on the board
VDDA: R16.2, R17.2, R18.2; also elsewhere on the board
V_HEAT: D18.1 (K), D19.1 (K), D20.1 (K), J18.1, J22.1, J23.1, Q10.2 (C), Q12.2 (C), Q14.2 (C), R13.1, R14.1, R15.1, R27.2, R28.2, R29.2; also elsewhere on the board
V_MOT: A1.9 (V_MOT), A2.9 (V_MOT), A3.9 (V_MOT), A4.9 (V_MOT), A5.9 (V_MOT), C2.2, C8.1, C19.1, C21.1, C23.1, D5.1 (K), D6.1 (K), J9.1, J10.1; also elsewhere on the board

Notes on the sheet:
Copyright NerdSmith.co.uk 2020. This source describes Open Hardware and is licensed under the CERN-OHL-Pv2 You may redistribute and modify this documentation and make products using it under the terms of the CERN-OHL-P v2 (https:/cern.ch/cern-ohl). This documentation is distributed WITHOUT ANY EXPR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

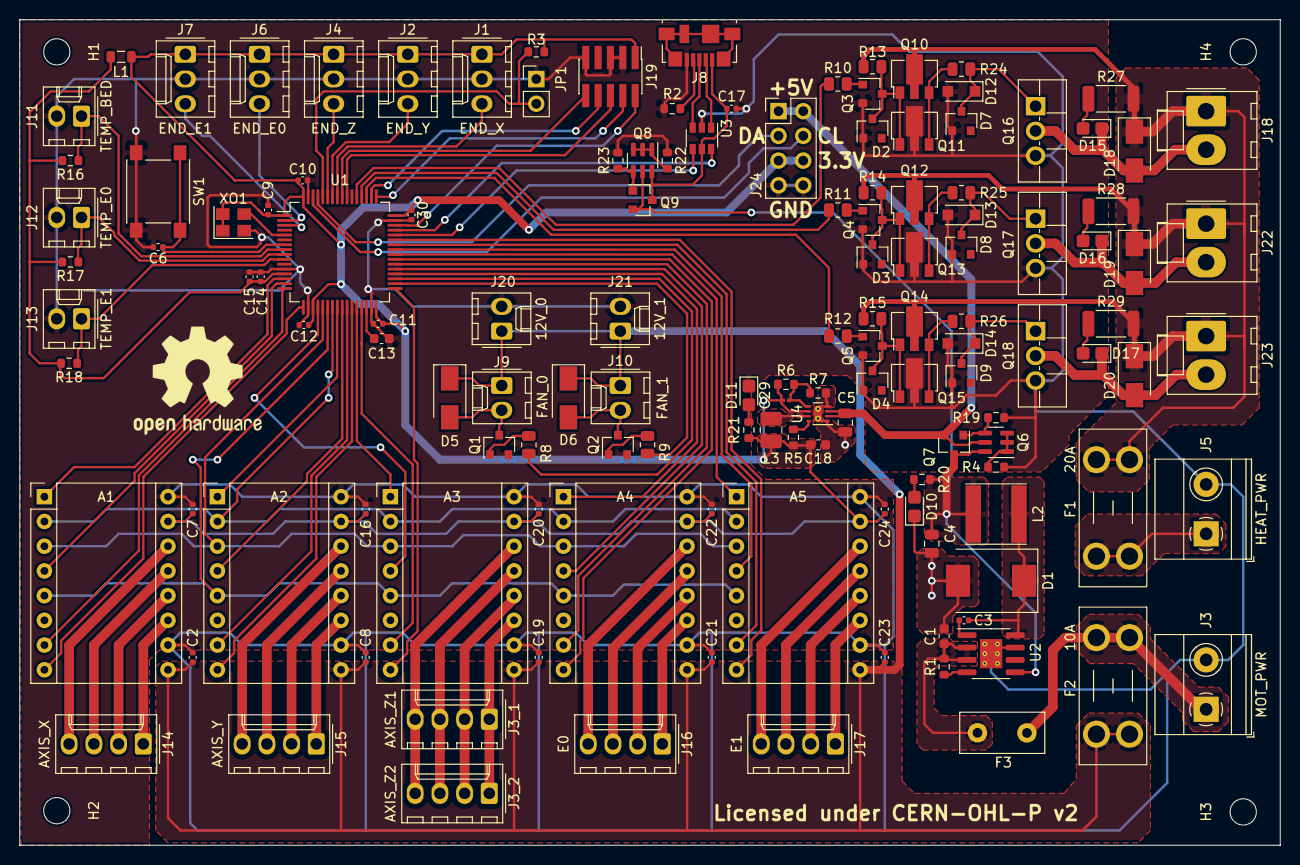
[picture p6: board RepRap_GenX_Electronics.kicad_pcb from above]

Board: 2 copper layers, 129.5 x 84.8 mm, 142 parts (0 on the bottom side), 117 nets.

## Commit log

2021-01-19 Added 3D render of board
2021-01-19 Added Circuit schematic in more convenient .pdf format
2021-01-21 Added ZVD and 5V breakout for external supply
    [RepRap_GenX_Electronics.kicad_pcb, RepRap_GenX_Electronics.sch]
2021-01-26 Added totem pole drivers for MOSFETs and split main schematic
    [MCU Devices.sch, RepRap_GenX_Electronics.kicad_pcb, RepRap_GenX_Electronics.sch]
2021-01-28 Added I2C and 3.3v breakout for expansion port
    [MCU Devices.sch, RepRap_GenX_Electronics.kicad_pcb, RepRap_GenX_Electronics.sch]

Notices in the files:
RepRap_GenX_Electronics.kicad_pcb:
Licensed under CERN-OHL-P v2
